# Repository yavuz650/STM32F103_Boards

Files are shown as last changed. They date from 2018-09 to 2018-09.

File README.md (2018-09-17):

# STM32F103 Boards
Rocket avionic boards, powered by the STM32F103C8T6 MCU.

This repository contains files and documentations of two avionic boards designed and developed for the Rocket Technologies Group of Istanbul Technical University in the year 2018. 

## Igniter Board
This board is designed to gather altitude data and control rocket's parachute deployment system. It was designed and programmed by Yavuz Selim Tozlu, assisted by Umit Yelken and L. Emre Top of Rocket Technologies Group.

## GPS Board
This board is designed to gather GPS data during flight, process it and send it to the ground station via the RF module attached to it. It was designed and programmed by Yavuz Selim Tozlu. 

Shout out goes to our [sponsor](http://www.megasistem.net) who was kind enough to manufacture the boards.

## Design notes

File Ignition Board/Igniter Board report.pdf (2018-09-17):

# STM32 Based

# Rocket Igniter Board

# Table of Contents

Preface | 3
Disclaimer | 3
About this document | 3
Feedback | 3
Further Reading | 3
PART A | Introduction to the board | 4
Chapter A1 | Purpose of this board | 5
Chapter A2 | Design process | 5
Chapter A3 | Board properties | 7
Chapter A4 | Post-manufacturing | 7
PART B | Embedding the STM32 MCU | 12
Chapter B1 | MCU Selection – Why STM32F103? | 13
Chapter B2 | External Circuitry | 13
Chapter B3 | Board Design | 15
PART C | Ignition Circuit | 17
Chapter C1 | The Circuit | 18
Chapter C2 | Safety Measures | 19
Chapter C3 | The Flaw | 19
PART D | Power Supply | 20
Chapter D1 | Step Down Regulator | 21
Chapter D2 | Linear Regulator and Power Switch | 21
PART E | Miscellaneous Parts | 22
Chapter E1 | MS5611 Barometer | 23
Chapter E2 | SD-Card Socket and Buzzer | 23
Final Words and Remarks | 24
About the Author | 24

# Preface

## Disclaimer

This document is written purely for guidance purposes. It is not written or verified by a professional. Everything shared in this document are of my own experience and observations. Therefore, the information might be incorrect or inaccurate. Reader must fully acknowledge this before moving forward.

## About this document

The purpose of this document is to share the experience and observations that were gathered during the design of this board with public, in order to ease hardware development for future generations. There is no exact target audience; students, hobbyists, even professionals may benefit from this. However, this document assumes the reader has basic knowledge of PCBs and electronics.

Release date: September, 2018

## Feedback

Any feedback related to the document or the design is welcome. Feel free to ask questions, suggest changes or improvement. Please direct your inquiries to tozlu16@itu.edu.tr.

## Further reading

Most of the knowledge in this document is derived from manuals and application notes from various companies. Below are the essential manuals and datasheets.

- https://www.st.com/resource/en/application_note/cd00164185.pdf
- https://www.st.com/resource/en/datasheet/cd00161566.pdf
- https://www.st.com/resource/en/reference_manual/CD00171190.pdf
- https://www.alldatasheet.com/datasheet-pdf/pdf/880802/TEC/MS5611-01BA03.html (https://www.alldatasheet.com/datasheet-pdf/pdf/880802/TEC/MS5611-01BA03.html)
- http://www.ti.com/lit/ds/symlink/lm2596.pdf

# PART A

# Introduction to the board

## A1) Purpose of this board

The Igniter Board was designed and developed for the Rocket Technologies Group of Istanbul Technical University. The board was designed to be included in the avionic bay of a rocket, and it eventually did fit inside the bay perfectly.

Its goal was to control and enable the deployment of the rocket’s parachute. The deployment process begins by estimating the altitude using the on-board embedded barometer. Upon reaching 20 meters below the apogee point, the board ignites two ignition wires, which in turn ignite an amount of black powder which ejects the surrounding body of the rocket to allow the parachute to be deployed.

Aside from ignition, it features a UART bridge, which is used to transmit altitude data, to another board in the bay.

## A2) Design process

The board consists of the following segments; MCU, barometer, ignition circuits, regulators and miscellaneous parts. All the drawings were done in Autodesk® Eagle 8.6.0. You might need 8.6.0 or later versions to open the board files.

The proper way of doing the schematic designs is to split the board up into modules like I did above, then work on modules, rather than working on the whole schematic all at once. For instance, I first drew the schematics of the MCU and did not move on to another part until I was done with it. After completing the MCU, I moved on to the regulators and so on. Modularizing the board makes it easier to maintain and manage the parts.

For this board, schematic design was basically reading and following the manuals. For this job, you will stick to the manuals that I shared in the preface section. Those manuals contain almost all the information you would need. The board layout, however, was somewhat trickier.

Due to budget limitations, the board had to be two-layered. Because of this, both layers had to contain a power plane and signal tracks. I decided to fill the top plane with GND and bottom plane with VDD. With this design, I ended up with a bunch of isolated sub-planes, as the signal tracks interrupt the power plane on that layer. Therefore, I routed lots of new, wide tracks that connect all the isolated planes with the main power plane. This is the problem with two-layered boards; dedicated layers for power planes are unavailable, instead power planes that are frequently interrupted by signal tracks must suffice. ST suggests to use at least a four-layered board to avoid this, though this two-layered board worked just fine.

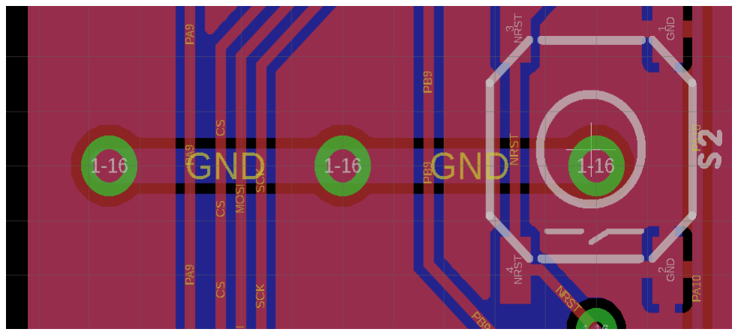
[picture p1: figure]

Figure 1: 0.8mm GND track routed to connect isolated planes

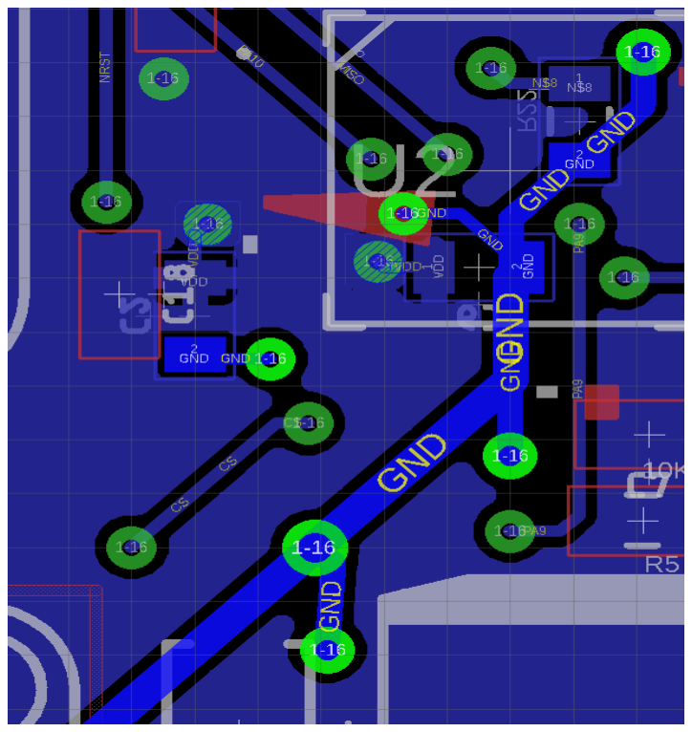
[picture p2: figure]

Figure 2: 0.7mm GND track routed to connect isolated planes

Layout of the parts was also challenging. Since the board was going to be housed in a rocket, I had very limited space. I had to keep the board as small as possible while also delivering the requirements. Finding the most optimized layout took several trials and errors, though it still is not perfect. My way of doing this was laying out and routing the MCU parts first, then moving on to ignition circuit and other miscellaneous parts. Throughout this process, I occasionally found myself having routing issues, this forced me to place parts on the bottom layer, as well as redesigning entire segments of the board. Ultimately, I managed to develop an optimal layout.

All the resistors and capacitors are of 0805 package. The only reason for this is that 0603 package is difficult to solder by hand, whereas 0805 is easier and also small enough for this board.

## A3) Board properties

- Board size | 69.50mm x 85.00mm
- Board thickness | 0.8mm, two-layered.
- Material | FR-4
- Soldermask | Green
- Track thickness | 1 oz (35um)

## A4) Post-manufacturing

Following images represent the three main phases of this board’s production in order; computer drawing, manufactured board, soldered board.

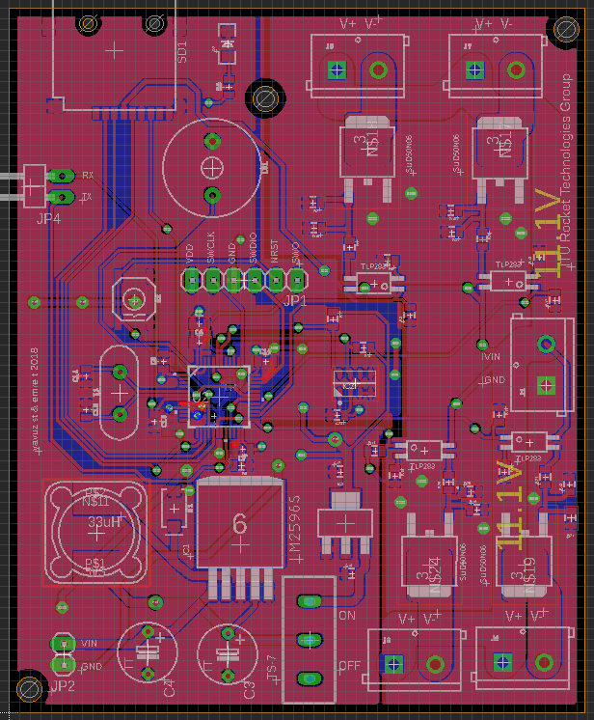
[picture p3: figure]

Figure 3: Computer drawing. Eagle 8.6.0

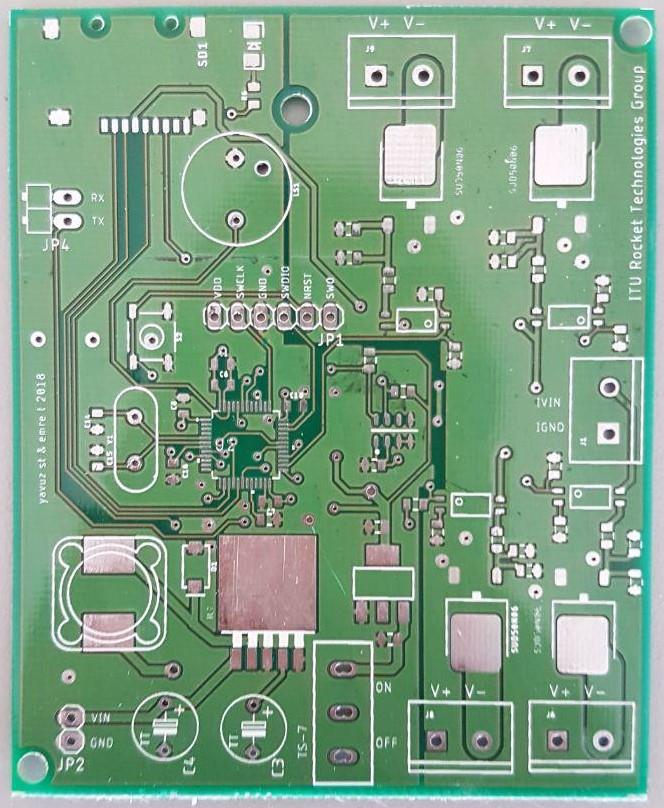
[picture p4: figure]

Figure 4: Manufactured board (top)

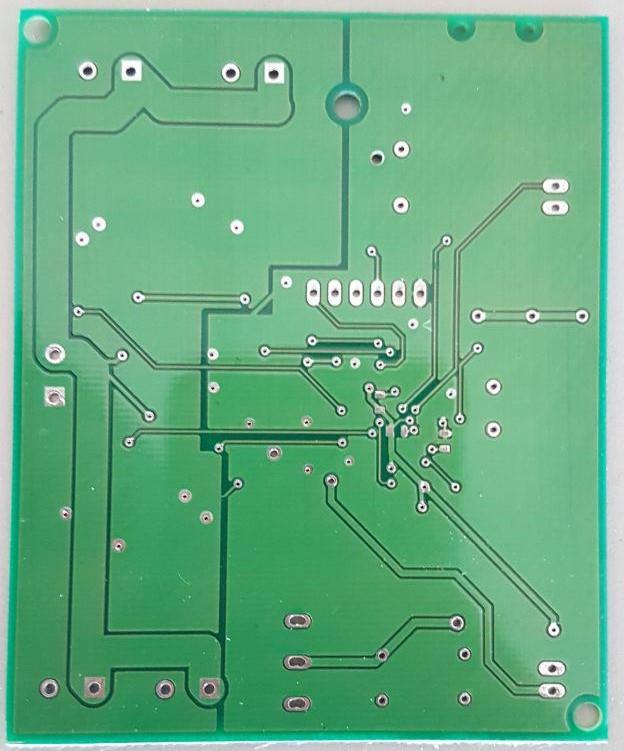
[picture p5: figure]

Figure 5: Manufactured board (bottom)

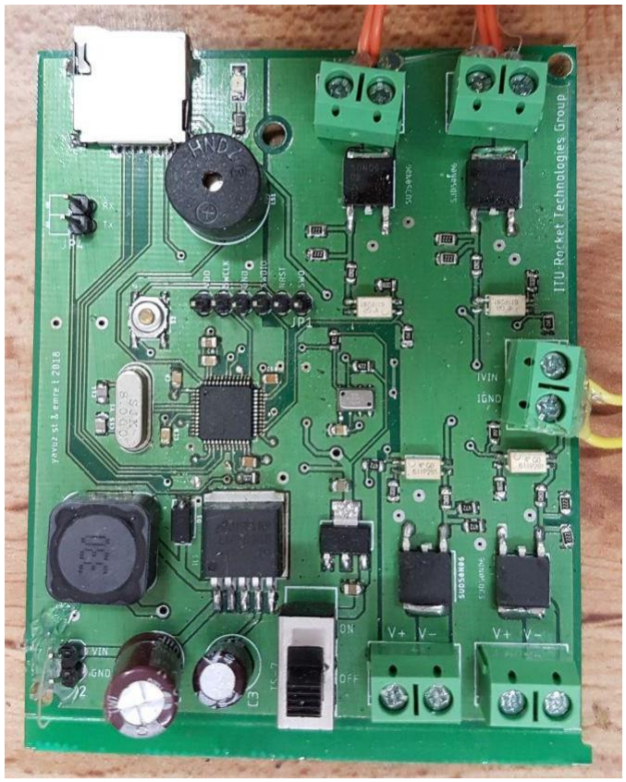
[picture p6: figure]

Figure 6: Soldered board (top)

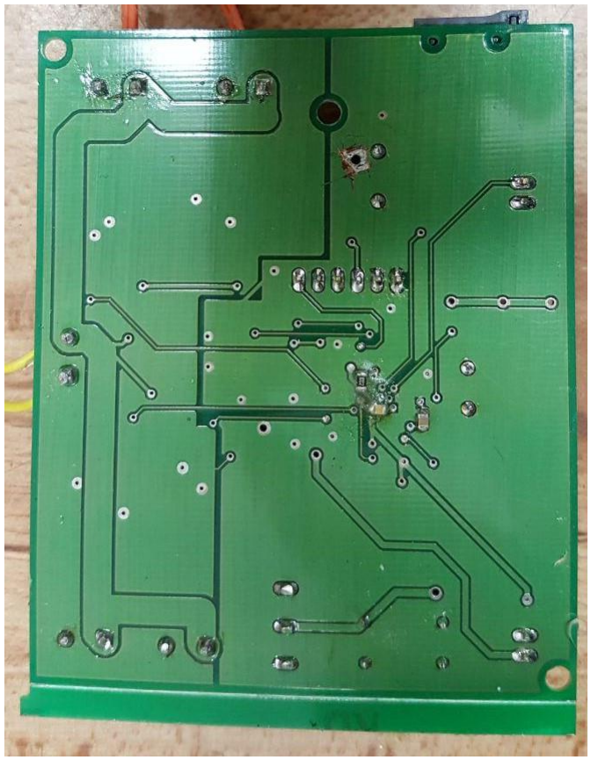
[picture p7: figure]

Figure 7: Soldered board (bottom)

This board is hand-soldered. There is visible flux residue left, especially on the bottom. I used Isopropyl alcohol to clean the top layer, perhaps due to the ingredients of my IPA, it left visible residue all over the board. An ESD safe brush was used to do the cleaning.

Reader may have noticed the hole with a scratched surrounding. That hole is a manufacturing flaw, it does not exist in the design. It is essentially a via that forms a conductive path between the top and the bottom layer, but around that area of the board, top layer is GND and bottom layer is VDD. This means that hole creates a short, this is why I had to scratch its surrounding copper to isolate it. I verified the short with a multimeter, checked all 6 boards that I received from the PCB house, all of them were suffering from the same flaw. This is a rare scenario where the PCB house manufactured defected boards.

# PART B

# Embedding the STM32 MCU

## B1) MCU Selection – Why STM32F103?

The main concerns during the MCU selection phase were; price, availability, software support, processing power, memory and physical size. At this point, options were quite clear; ATmega or STM32 – most common and easy to use MCUs in the market. Using ATmega was the easiest and the most reliable choice, however that would contradict with the idea of this project – which is to learn and experience new concepts, technologies. Today, developing projects with ATmega a.k.a. Arduino MCUs are incredibly simple, so much so that it merely gives people the illusion of actually developing something, which rarely is the case. This is mainly why the STM32 was chosen for this project.

The processing power that came with the STM32 was certainly not needed, neither was the memory, but the learning difference was immense.

Tools and libraries provided by ST incredibly eased up the software development phase, which placed STM32 above the other MCUs in the market.

## B2) External Circuitry

Minimum external parts to get the STM32 MCU working are; decoupling capacitors, a crystal, reset circuitry, boot pin configuration and SWD output. Note that, this is what ST suggests, indicating the MCU may work without some of those components. Also, an external crystal is not mandatory since the MCU offers an internal clock source. The drawbacks are that internal oscillator is less reliable, has more jittering and also less accurate than an external crystal.

Detailed information on decoupling caps can be found in the manual. To sum it up, for STM32F103C8T6 MCU, you would need; 5x 100nF, 1x 10uF, 1x 1uF decoupling capacitors to filter the power input. The MCU has 3 main power pairs, 1 analog power pair and 1 external battery input which should be connected to the VDD rail if not used.

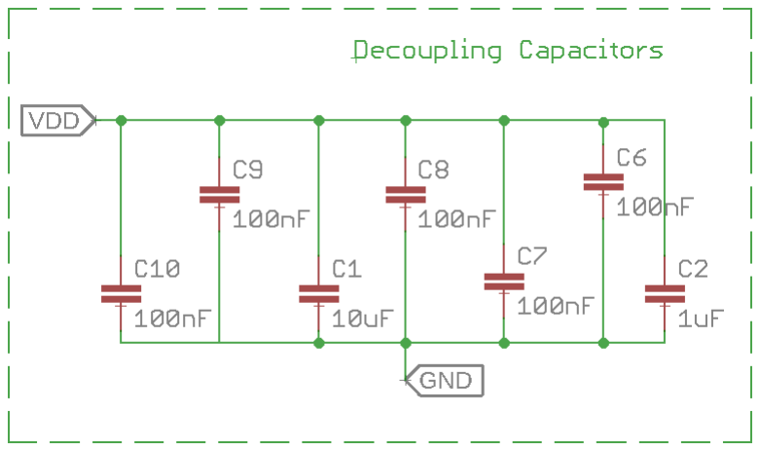
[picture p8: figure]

Figure 8: Decoupling capacitors for STM32F103C8T6

The memory block used to boot the MCU is determined by configuration of boot pins. Main flash memory is sufficient for most purposes, this project is no exception. Correct boot pin configuration for main flash memory is achieved when both boot pins are in low state, in other words, pulled to low. The manual suggests to use 10kOhm resistors as pull-downs.

In order to give the user the option to alter the boot mode between different memory blocks, designer can attach jumpers to the boot pins. Since this would take extra space on the board, I decided to strictly pull the pins low. Detailed information on boot pins can be found on the manual.

Igniter board houses an external crystal for the STM32 MCU. There is no guidance as to what the proper frequency would be, therefore an 8MHz crystal is used. The important thing here is to match the crystal’s frequency value with the value in your code during software development. Any value from 15pF to 22pF for load capacitors would be fine.

Reset circuitry is also described in the manual. Implementation for this board is shown in the following image.

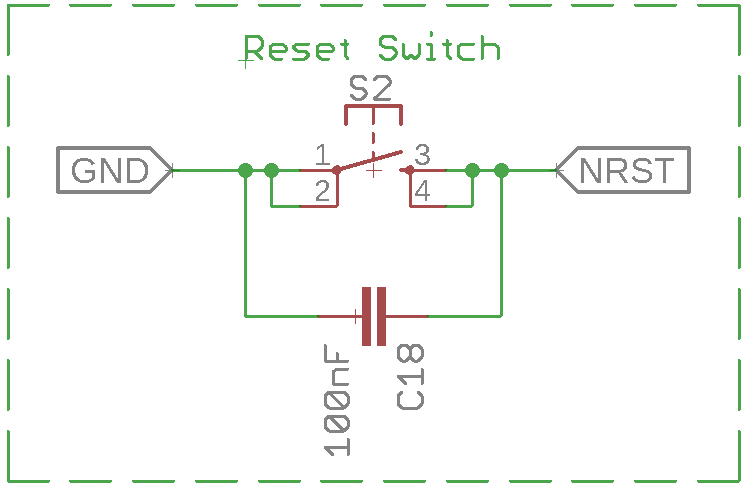
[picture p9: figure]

Figure 9: Reset Circuitry. NRST is tied to NRST pin of the MCU

As an interface between the MCU and the computer, Serial Wire Debug is used. Normally, SWD requires 3 pins; SWCLK, SWDIO, RST, aside from a common ground. On the Igniter Board, there are 2 additional pins; VDD and SWO.

VDD pin is added so that the board could be powered without having to use the main power supply of the board. This way I could power, program, debug the MCU without having to provide an external power source, which was really helpful during the programming and the testing phase.

SWO pin is an extra debugging feature offered by the SWD interface. Although it exists on the board, SWO pin was never used.

## B3) Board Design

There are lots of guides on placement of decoupling capacitors. Following image is taken from ST’s manual and suggests the most ideal placement, which I attempted to follow.

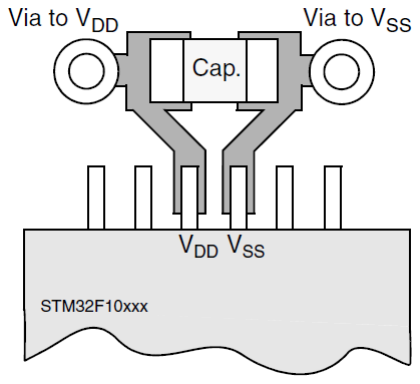
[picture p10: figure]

Figure 10: Ideal capacitor placement

To achieve this placement for each and every capacitor on a two-layer board is simply impossible, it is not required either. The idea is to keep the tracks as short and wide as possible, maintaining a low impedance. Also, both layers can be used to place those capacitors. On the Igniter Board, all the tracks entering the MCU are 0.25mm wide.

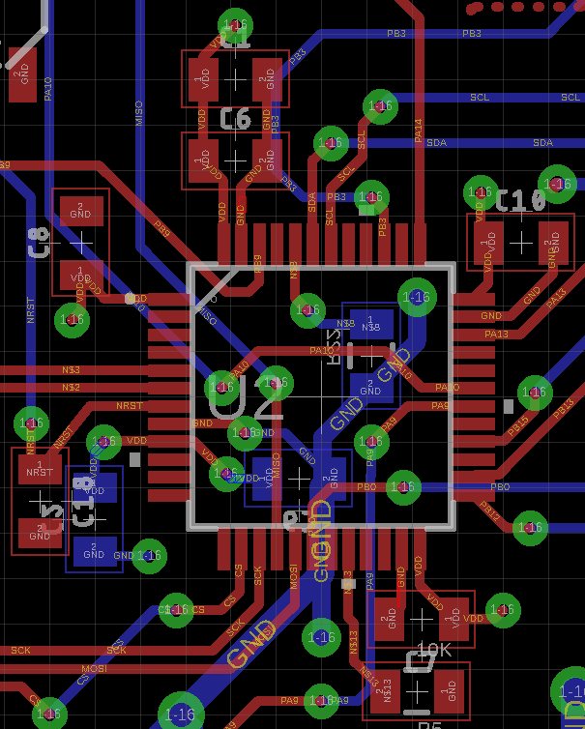
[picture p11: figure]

Figure 11: Circuitry around the STM32 MCU. Capacitors and resistors.

For the crystal, I kept it as close as possible to the MCU, while keeping the tracks and the load capacitors symmetric.

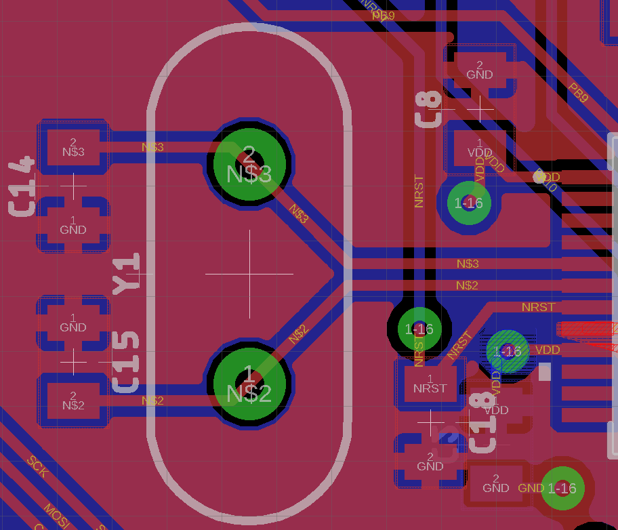
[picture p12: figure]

Figure 12: Symmetric tracks and capacitors for the crystal

It can be stated that the STM32 MCU was embedded properly and successfully on this board. No stability issues, timer inaccuracy or any other unexpected behavior were observed.

# PART C

# Ignition Circuit

## C1) About the circuit

Ignition circuit is the electronic system that controls the ejection of the rocket. Due to the nature of its task, it is crucial that the system is fail-safe. Thus, it is equipped with an array of components to attain the level of safety required. The last thing needed on the field is a rocket ejecting at the wrong time, in the wrong place i.e. on the ground. It must be noted that this circuit has an enormous flaw that will be addressed soon.

Following is an image of the schematic of the circuit.

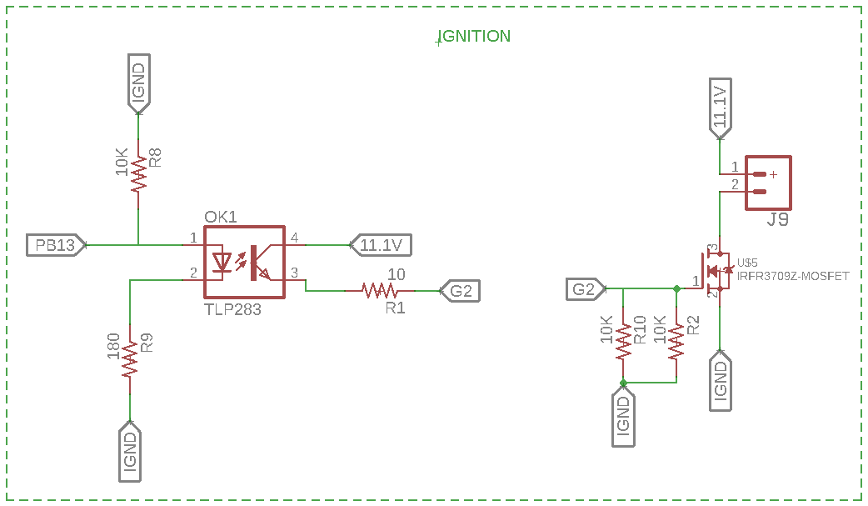
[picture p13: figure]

Figure 13: Ignition Circuit schematic

The circuit consists of two main stages: The opto-coupler and the N-MOSFET. Input of the opto-coupler’s LED is connected to the MCU’s pin PB13 in this case. The chain of events is triggered as the MCU drives the associated pin high, which activates the opto-coupler and ties 11.1V to the MOSFET’s gate. Applying voltage to the MOSFET’s gate allows current to flow from the drain to the source. Finally, this current flows through the terminal placed in between the drain and the source. Ignition wire that is attached to the terminal is ignited by this very current.

The circuit is powered directly from a 11.1V Li-Po battery, and has a separate ground(IGND). Cables for power input are attached to a terminal, since common pin headers cannot handle the power delivered by the battery.

During the ignition of the wire, current draw can go up to 5A. Thus, MOSFET used in this circuit must be able to handle currents up to 5A, voltages up to 12V. The MOSFET used in this board is SUD50N06 from Vishay.

## C2) Safety Measures

The ignition circuit is required to be electrically isolated from the rest of the board, as noise might cause the opto-coupler or the MOSFET to get activated or prevent them from getting activated, despite this is unlikely. Any possible kind of electrical interference between the circuit and the rest of the board is unwanted. This requirement led to the use of an opto-coupler. This way, the ignition circuit and the rest of the board do not have to share a common ground.

The input of the opto-coupler and the gate of the MOSFET are pulled to low. These pins cannot be left floating as this could lead to unintended activation of the components. Those pull-down resistors cannot be omitted. Notice, not one, but two pull-down resistors are attached to the gate of the MOSFET for further safety.

## C3) The Flaw

The design of this circuit contradicts with one of the main requirements discussed above, which is electrical isolation between the circuit and the rest of the board. Careful eyes may have noticed this just by looking at the schematic given at the beginning of this part.

The output of the diode inside the opto-coupler is tied to IGND through a resistor, whereas it should have been tied to GND. The reason can be obvious, the MCU’s 3.3V logic level is defined with respect to GND, not IGND. Then, only way to make this circuit work is to tie GND and IGND together, which makes the entire circuit pointless and redundant. Unfortunately, there is no alternative solution, and that is the work around I followed with my circuit.

Also, notice the pull-down resistor attached to the input of the opto-coupler pulls the pin to IGND, not GND –which is another flaw.

Nevertheless, this circuit did work with no problems, and successfully ejected the rocket’s body at the desired altitude.

Following is the corrected version of the circuit.

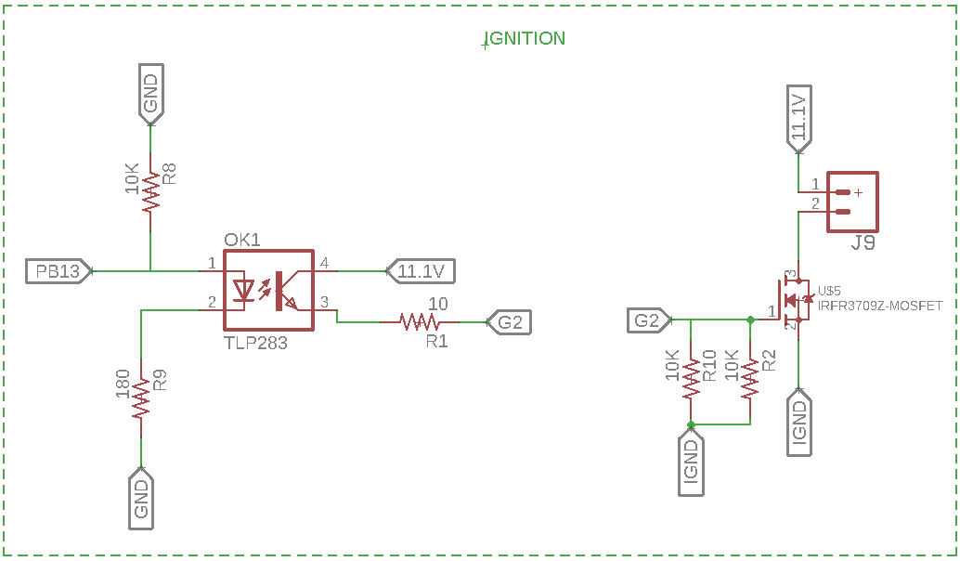
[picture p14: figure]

Figure 14: Corrected circuit.

# PART D

# POWER SUPPLY

## D1) Step Down Regulator

The input voltage for the circuit is planned to be 7.4V from a Li-Po battery. Target voltage is 3.3V. This leaves us two options, a linear regulator or a step down regulator. Regulating 7.4V to 3.3V with a bare linear regulator is very inefficient and slightly risky. Instead, I embedded a step down regulator to drop the 7.4V to 5V and use a linear regulator thereafter.

The step down regulator is based on the LM2596 from TI. The circuitry around it consists of an inductor, two aluminum capacitors and a schottky diode. This is also the suggested circuit in the datasheet.

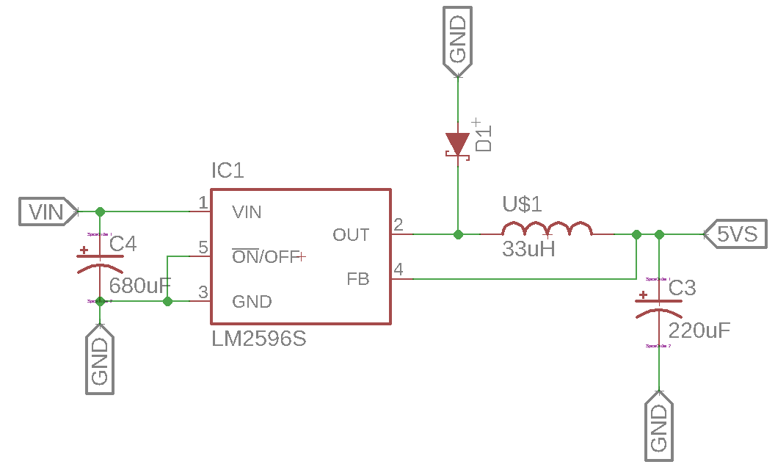
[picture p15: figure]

Figure 15: Step down regulator circuit, based on LM2596

There is no significant reason to use aluminum capacitors for this circuit, however, they are cheap and easily available.

As for the layout, TI pointed out some information in the datasheet, the rule of thumb is to keep the traces as wide as possible and the external circuitry close to the LM2596 IC.

## D2) Linear Regulator and Power Switch

To achieve the target voltage, a linear regulator is used to drop 5V to 3.3V. The linear regulator used in this board is AMS1117 from ams-semitech.

There is also a slide switch added to the board. This switch controls the whether the MCU side of the circuit is powered or not, it has nothing to do with the ignition circuitry.

There is a minor, yet silly design flaw about the switch’s placement. The current to the circuit enters the switch after it goes through the step down regulator. This means, the regulator is powered on and is working no matter what the state of the switch might be. This is why the switch should have been placed right after the power jack to function as it was intended.

It can be seen that the holes for the slide switch are not circular, as they usually are. They are rather oblong holes. This is a very important detail about the package of the switch. I drew the board symbol of the switch myself, mainly because there were no matching libraries. To draw oblong holes in Eagle, one has to use the “milling layer” in Eagle. The oblong hole should be drawn on the milling layer, and must be included in the gerber files that will be sent to the PCB house.

# PART E

# MISCALLENOUS PARTS

## E1) MS5611 Barometer

The board houses an MS5611 digital barometer from TE Connectivity. Its only task is to measure the air pressure, then convert it to an altitude value.

Schematic of the barometer includes a mere capacitor, and 2 I2C pull-up resistors, as is suggested by its datasheet.

The primal challenge with the barometer is, in fact, in the software side. That is, implementing C code for the communication between the STM32 MCU and the sensor. Enough information on software development with MS5611 is given on the datasheet. However, to realize a properly working interface takes some effort. A working library based on the HAL drivers from ST is shared in the repository.

## E2) SD Card Socket and Buzzer

One of the requirements of the igniter board was to save flight data to a micro-SD card attached to the board. However, despite many attempts, I never managed to establish a fully working interface between the MCU and the micro-SD card. Therefore, it is unknown whether the socket circuitry works at all. In spite of this, since it imitates working designs, I would expect it to function properly if a working interface is supplied.

The buzzer is a very specific component required due to the board’s purpose being related to the rocketry. Basically, when the rocket successfully lands on the ground, it needs to be located and retrieved by the team. Buzzer is added so that the sound it makes can be helpful to locate the parts.

There is a personal remark I would like to add about the buzzer’s circuitry. The buzzer is controlled and powered directly by the STM32 MCU. This is not the best way to do this, as the voltage supplied by the MCU is very low, 3.3V. Note that, the volume of the sound the buzzer makes is directly proportional to the voltage applied to its pins. Thus, a higher voltage is preferable in this case. To achieve this, a simple BJT can be used, with its base pin connected to the MCU.

## Final Words and Remarks

The development of this board involves months of research, a manufactured but unsuccessful board design, and lots of trials and errors. The very beginning of this process goes back to February of the year 2018. The board was successfully manufactured around July, 2018. This document is written during September, 2018.

It can be concluded that the board is successful. It was programmed, debugged, powered on and off many times, and has worked in a stable manner. It successfully gathered pressure and altitude data, ejected the rocket properly, as was intended. Nevertheless, reader should pay attention to the flaws mentioned throughout this document.

Most of the omitted information about the design can be deduced by the reader by carefully examining the board files.

Last but not least, the software that was used on this board for parachute deployment is shared in the repository.

## About the author

I am Yavuz Selim Tozlu, at the time of writing this paper, I am studying Electronics and Communication Engineering at Istanbul Technical University. E-mails in any regard can be sent to tozlu16@itu.edu.tr.

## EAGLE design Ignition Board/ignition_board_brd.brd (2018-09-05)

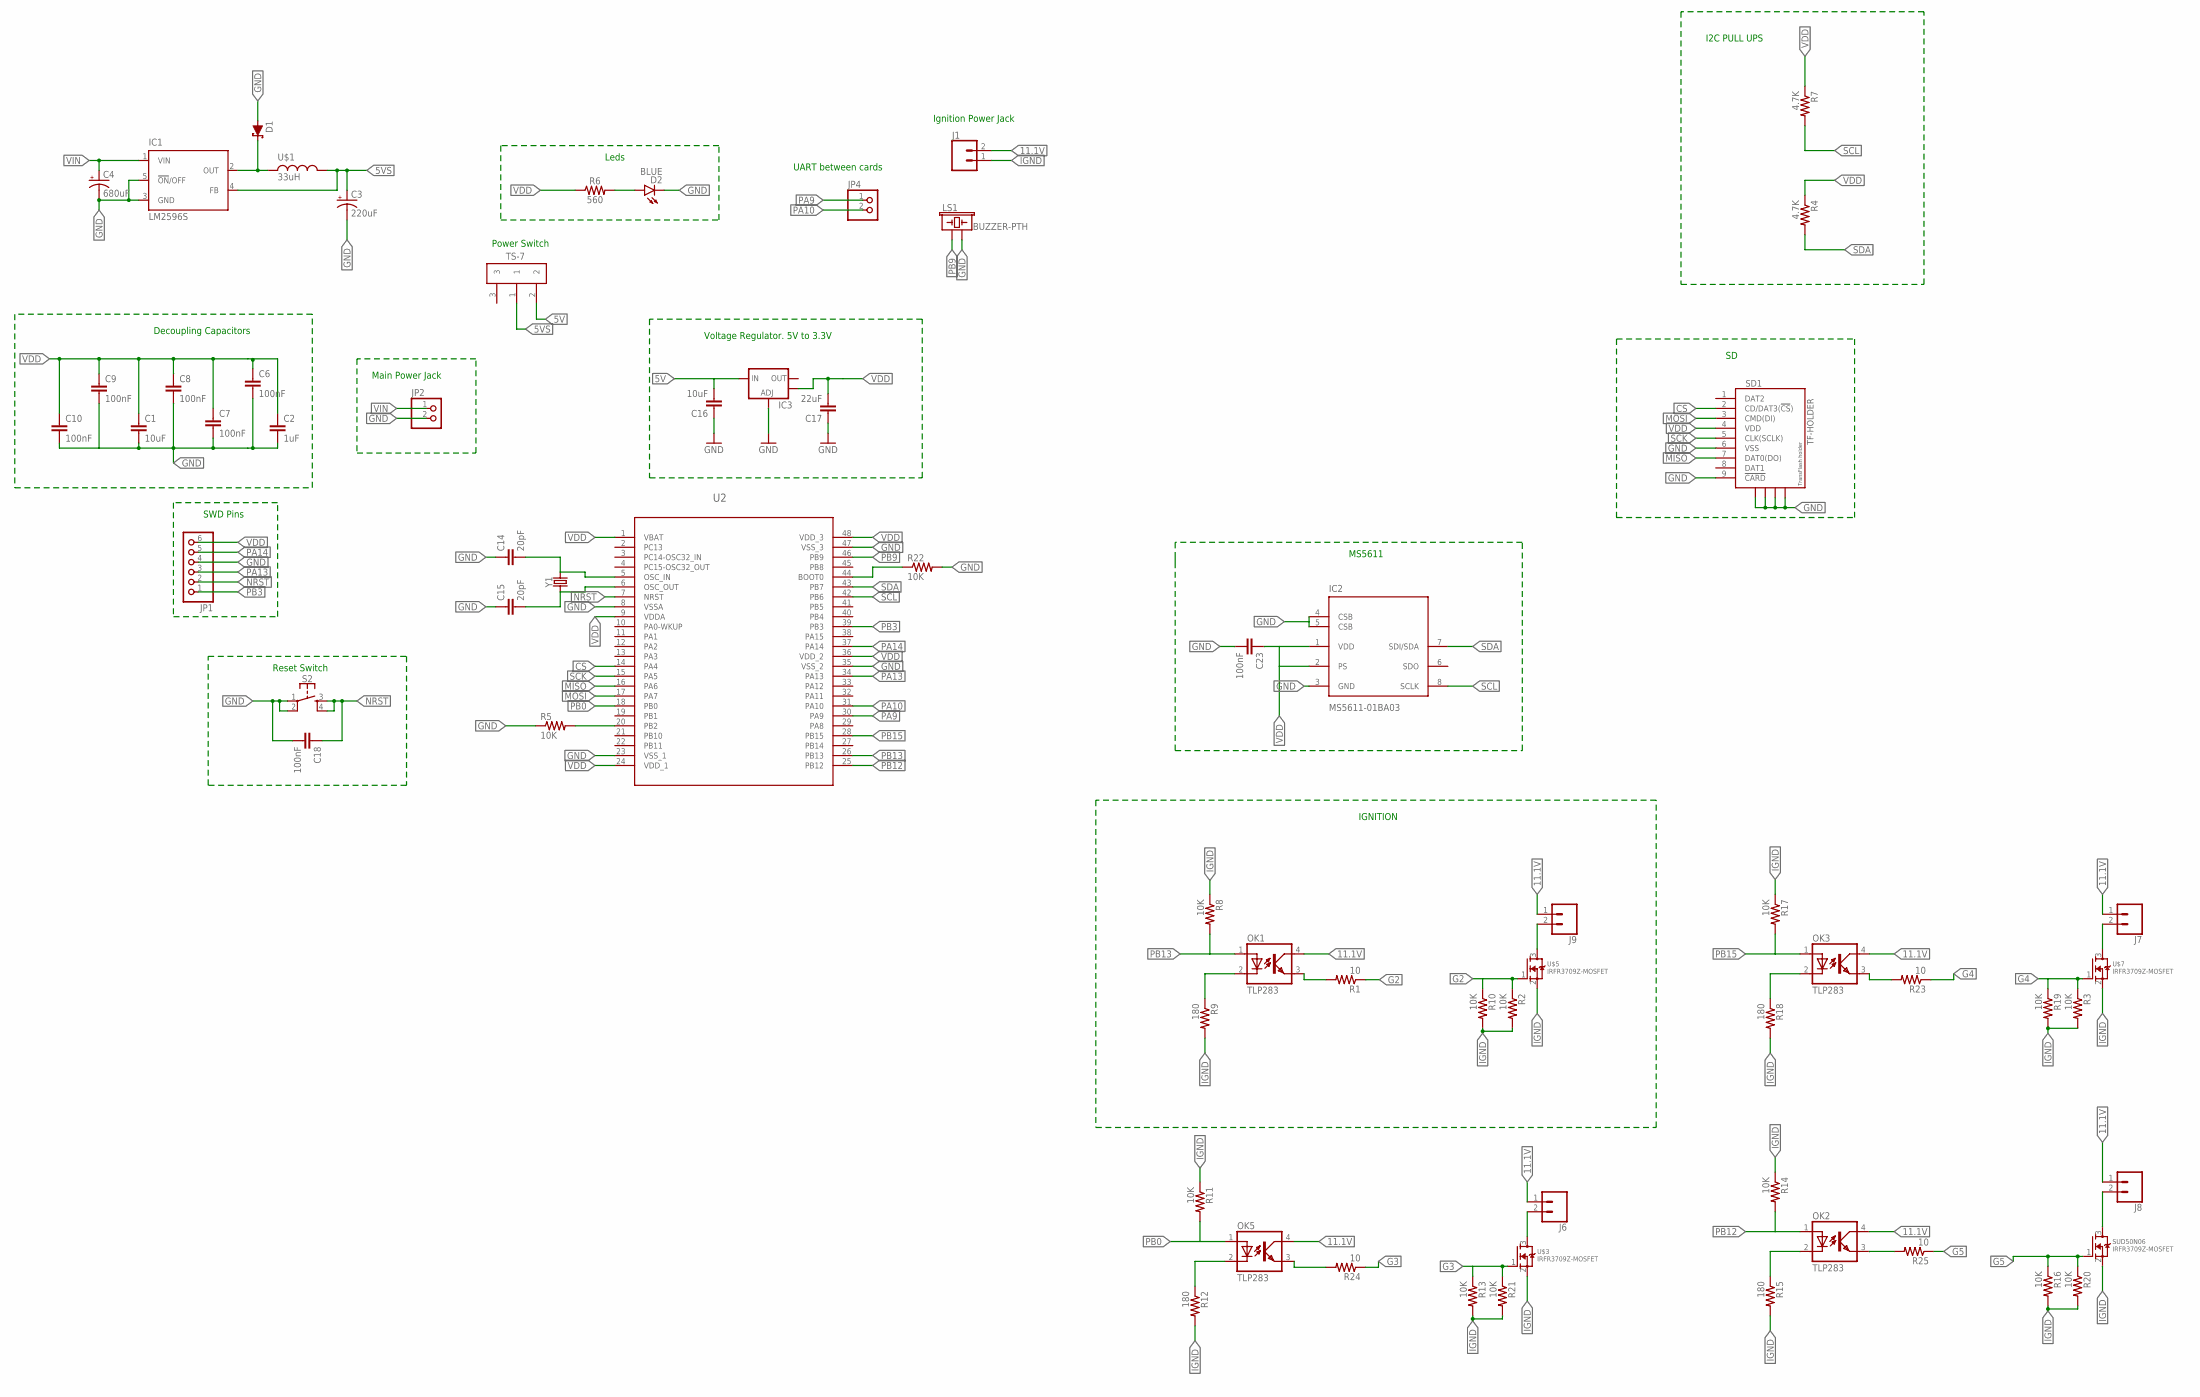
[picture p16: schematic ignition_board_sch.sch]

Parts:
C1: 10uF; 0805
C2: 1uF; 0805
C3: 220uF; TT5D7
C4: 680uF; TT5D7
C6, C7, C8, C9, C10, C18: 100nF; 0805
C14, C15: 20pF; 0805
C16: 10uF; 0805@2
C17: 22uF; 0805@2
C23: 100nF; 0805@2
D1: 3A/40V/500mV; SMA-DIODE
D2: BLUE; LED-1206
IC1: LM2596S; TO263-5
IC2: MS5611-01BA03; SON125P300X500X100-8N
IC3: V_REG_LM1117SOT223; SOT223
J1, J6, J7, J8, J9: CONN_025MM; SCREWTERMINAL-5MM-2
JP1: PINHD-1X6; 1X06
JP2: PINHD-1X2; 1X02
JP4: PINHD-1X2/90; 1X02/90
LS1: BUZZER-PTH; BUZZER-12MM
OK1, OK2, OK3, OK5: TLP283; MINI-FLAT-4
R1, R23, R24, R25: 10; 0805
R2, R3, R5, R8, R10, R11, R13, R14, R16, R17, R19, R20, R21, R22: 10K; 0805
R4, R7: 4.7K; 0805
R6: 560; 0805@1
R9, R12, R15, R18: 180; 0805
S2: MOMENTARY-SWITCH-SPST-2-SMD-5.2MM; TACTILE_SWITCH_SMD_5.2MM
SD1: TF-HOLDER; TF-PULL
SUD50N06: IRFR3709Z-MOSFET; TO252
TS-7: TS-7; TS7
U2: STM32F103CXT2; LQFP48-7X7MM
U$1: 33uH; MSS1260
U$3, U$5, U$7: IRFR3709Z-MOSFET; TO252
Y1: CRYSTALPTH-HC49US; HC49US

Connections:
5V: C16.2, IC3.3 (IN), TS-7.2
5VS: C3.+, IC1.4 (FB), TS-7.1, U$1.P$1
11.1V: J1.2, J6.1, J7.1, J8.1, J9.1, OK1.4 (COL), OK2.4 (COL), OK3.4 (COL), OK5.4 (COL)
CS: SD1.2 (CD/DAT3(!CS!)), U2.14 (PA4)
G2: R1.1, R2.1, R10.1, U$5.1 (G)
G3: R13.1, R21.1, R24.1, U$3.1 (G)
G4: R3.1, R19.1, R23.1, U$7.1 (G)
G5: R16.1, R20.1, R25.1, SUD50N06.1 (G)
GND: C1.2, C2.2, C3.-, C4.-, C6.2, C7.2, C8.2, C9.2, C10.2, C14.1, C15.1, C16.1, C17.1, C18.2, C23.2, D1.A, D2.C, IC1.3 (GND), IC1.5 (!ON!/OFF), IC2.3 (GND), IC2.4 (CSB), IC2.5 (CSB), IC3.1 (ADJ), JP1.4, JP2.2, LS1.- (2), R5.1, R22.2, S2.1, S2.2, SD1.6 (VSS), SD1.9 (!CARD), SD1.S1, SD1.S2, SD1.S3, SD1.S4, U2.8 (VSSA), U2.23 (VSS_1), U2.35 (VSS_2), U2.47 (VSS_3)
IGND: J1.1, R2.2, R3.2, R8.1, R9.2, R10.2, R11.1, R12.2, R13.2, R14.1, R15.2, R16.2, R17.1, R18.2, R19.2, R20.2, R21.2, SUD50N06.2 (S), U$3.2 (S), U$5.2 (S), U$7.2 (S)
MISO: SD1.7 (DAT0(DO)), U2.16 (PA6)
MOSI: SD1.3 (CMD(DI)), U2.17 (PA7)
unnamed: C15.2, U2.6 (OSC_OUT), Y1.1
unnamed: C14.2, U2.5 (OSC_IN), Y1.2
unnamed: R22.1, U2.44 (BOOT0)
unnamed: D1.C, IC1.2 (OUT), U$1.P$2
unnamed: OK1.3 (EMIT), R1.2
unnamed: R5.2, U2.20 (PB2)
unnamed: D2.A, R6.2
unnamed: OK2.3 (EMIT), R25.2
unnamed: J7.2, U$7.3 (D)
unnamed: J9.2, U$5.3 (D)
unnamed: J6.2, U$3.3 (D)
unnamed: OK3.3 (EMIT), R23.2
unnamed: OK5.2 (C), R12.1
unnamed: OK5.3 (EMIT), R24.2
unnamed: J8.2, SUD50N06.3 (D)
unnamed: OK2.2 (C), R15.1
unnamed: OK1.2 (C), R9.1
unnamed: OK3.2 (C), R18.1
NRST: C18.1, JP1.2, S2.3, S2.4, U2.7 (NRST)
PA9: JP4.1, U2.30 (PA9)
PA10: JP4.2, U2.31 (PA10)
PA13: JP1.3, U2.34 (PA13)
PA14: JP1.5, U2.37 (PA14)
PB0: OK5.1 (A), R11.2, U2.18 (PB0)
PB3: JP1.1, U2.39 (PB3)
PB9: LS1.+ (1), U2.46 (PB9)
PB12: OK2.1 (A), R14.2, U2.25 (PB12)
PB13: OK1.1 (A), R8.2, U2.26 (PB13)
PB15: OK3.1 (A), R17.2, U2.28 (PB15)
SCK: SD1.5 (CLK(SCLK)), U2.15 (PA5)
SCL: IC2.8 (SCLK), R7.2, U2.42 (PB6)
SDA: IC2.7 (SDI/SDA), R4.2, U2.43 (PB7)
VDD: C1.1, C2.1, C6.1, C7.1, C8.1, C9.1, C10.1, C17.2, C23.1, IC2.1 (VDD), IC2.2 (PS), IC3.4 (OUT), JP1.6, R4.1, R6.1, R7.1, SD1.4 (VDD), U2.1 (VBAT), U2.9 (VDDA), U2.24 (VDD_1), U2.36 (VDD_2), U2.48 (VDD_3)
VIN: C4.+, IC1.1 (VIN), JP2.1

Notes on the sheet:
Decoupling Capacitors
Voltage Regulator. 5V to 3.3V
Main Power Jack
Reset Switch
Leds
SWD Pins
MS5611
IGNITION
I2C PULL UPS
UART between cards
Power Switch
Ignition Power Jack

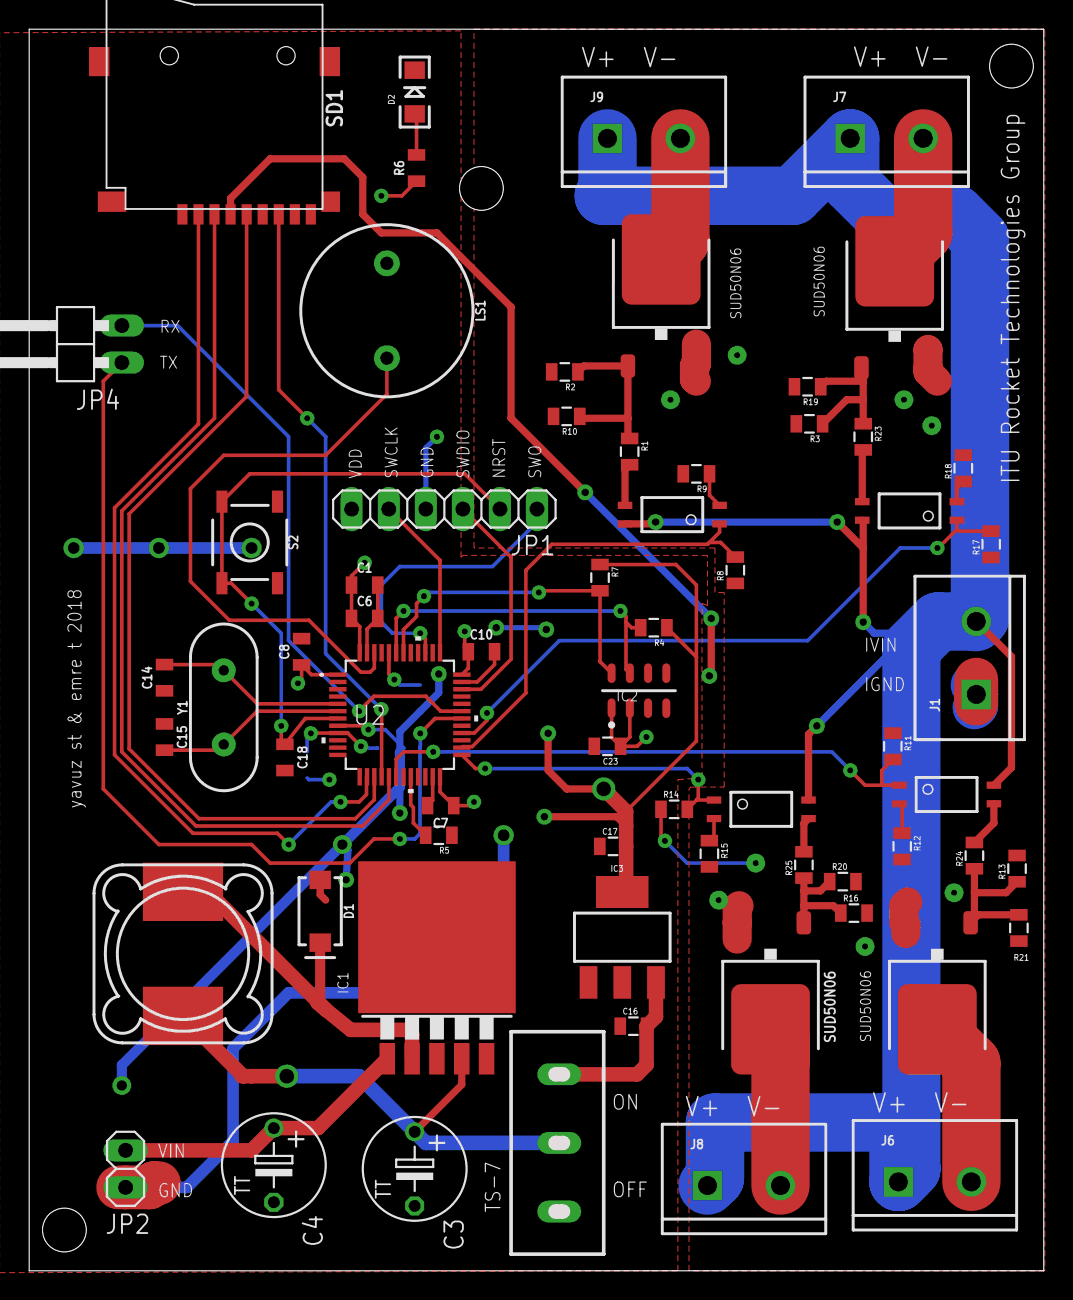
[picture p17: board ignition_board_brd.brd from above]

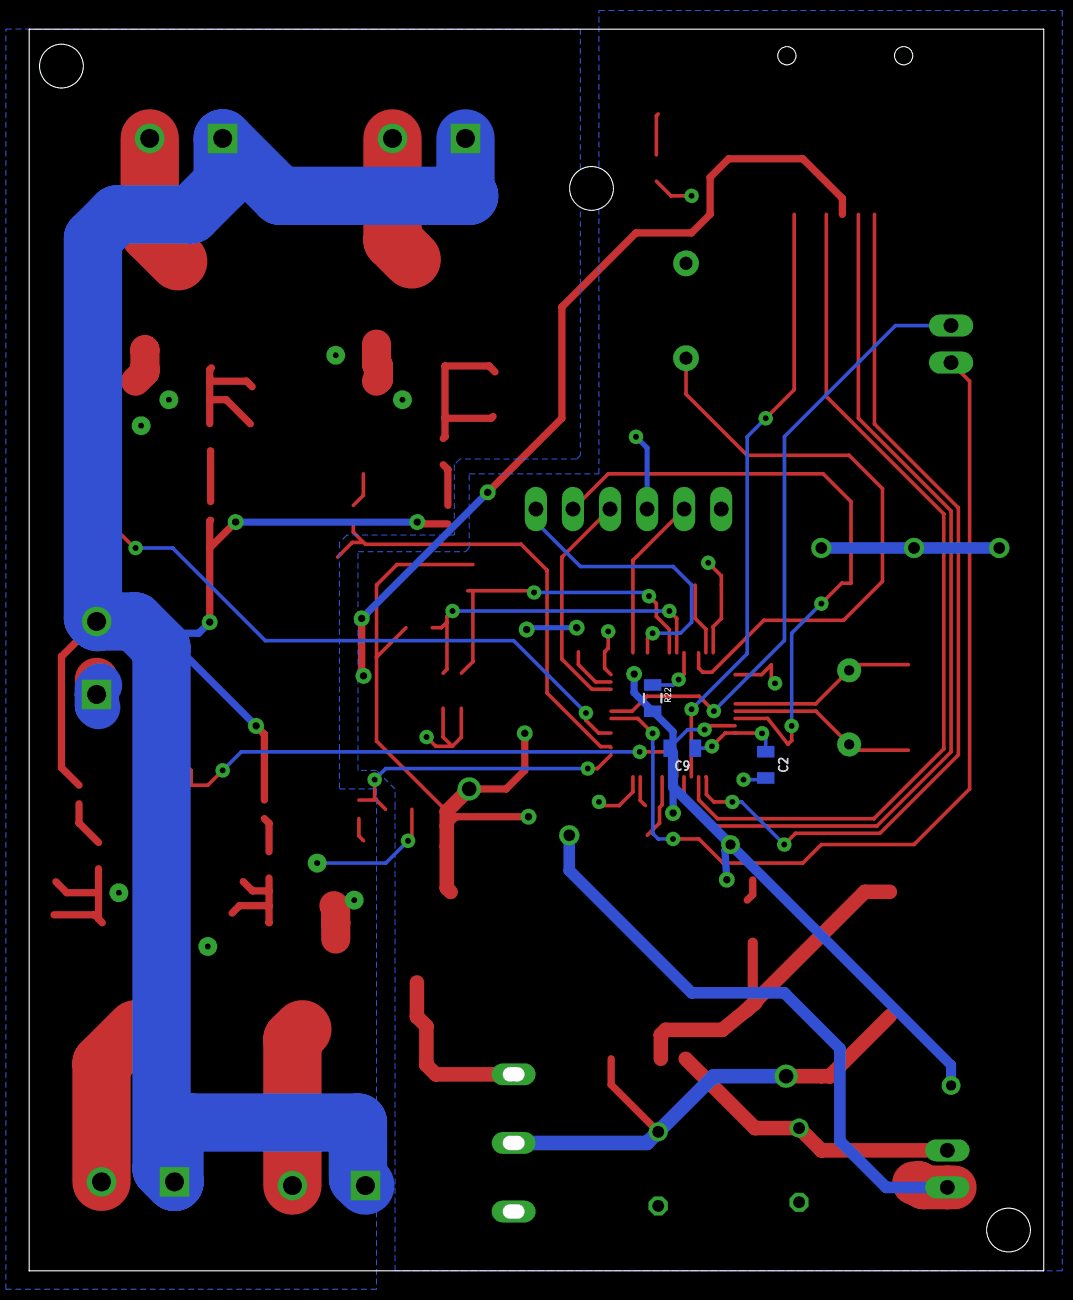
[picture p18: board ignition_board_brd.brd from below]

Board: 2 copper layers, 69.5 x 85.1 mm, 68 parts (3 on the bottom side), 46 nets.

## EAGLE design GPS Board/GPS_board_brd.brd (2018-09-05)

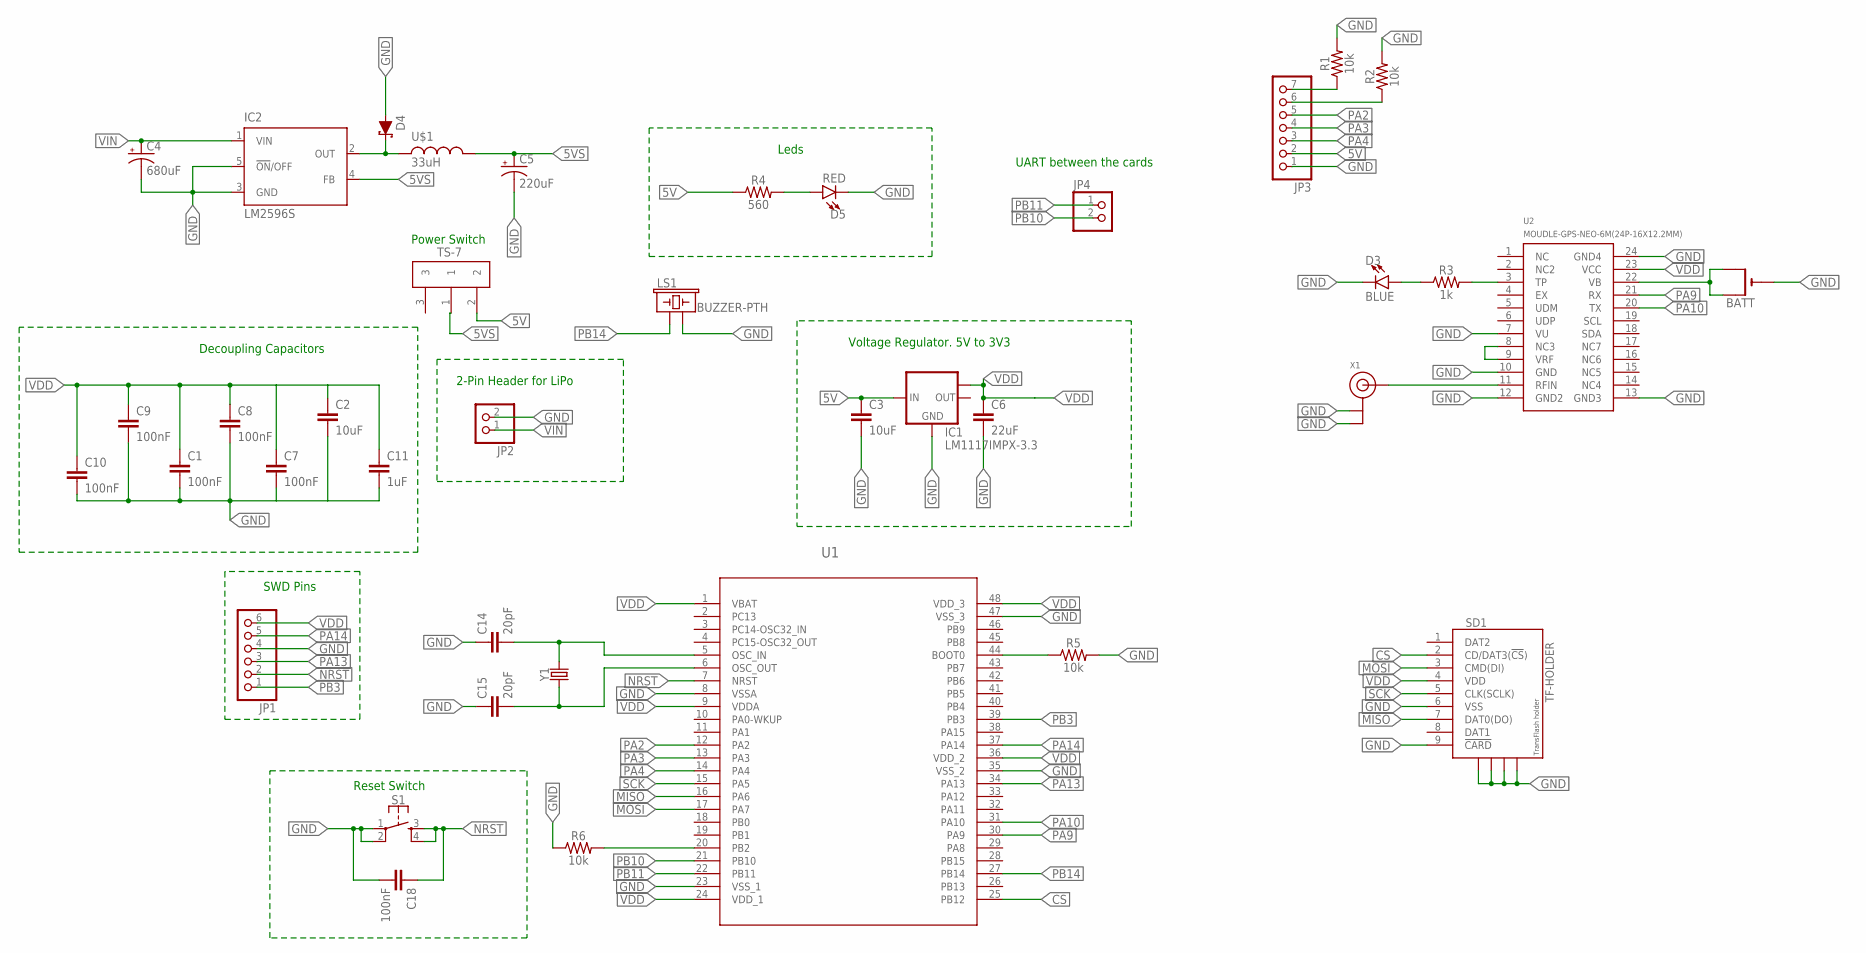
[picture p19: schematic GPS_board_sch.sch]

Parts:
BATT: CR1220SMT; CR1220-SMD
C1, C7, C8, C9, C10, C18: 100nF; 0805
C2, C3: 10uF; 0805
C4: 680uF; TT5D7
C5: 220uF; TT5D7
C6: 22uF; 0805
C11: 1uF; 0805
C14, C15: 20pF; 0805
D3: BLUE; LED-1206
D4: 3A/40V/500mV; SMA-DIODE
D5: RED; LED-1206
IC1: LM1117IMPX-3.3; SOT223
IC2: LM2596S; TO263-5
JP1: PINHD-1X6; 1X06
JP2: PINHD-1X2; 1X02
JP3: PINHD-1X7; 1X07
JP4: PINHD-1X2/90; 1X02/90
LS1: BUZZER-PTH; BUZZER-12MM
R1, R2, R5, R6: 10k; 0805
R3: 1k; 0805
R4: 560; 0805
S1: MOMENTARY-SWITCH-SPST-2-SMD-5.2MM; TACTILE_SWITCH_SMD_5.2MM
SD1: TF-HOLDER; TF-PULL
TS-7: TS-7; TS7
U1: STM32F103CXT2; LQFP48-7X7MM
U2: MOUDLE-GPS-NEO-6M(24P-16X12.2MM); GPS24P-SMD-1.1-16X12.2MM
U$1: 33uH; MSS1260
X1: ANTENNA_U.FL; U.FL
Y1: CRYSTALPTH-HC49US; HC49US

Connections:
5V: C3.1, IC1.3 (IN), JP3.2, R4.1, TS-7.2
5VS: C5.+, IC2.4 (FB), TS-7.1, U$1.P$1
CS: SD1.2 (CD/DAT3(!CS!)), U1.25 (PB12)
GND: BATT.-, C1.2, C2.2, C3.2, C4.-, C5.-, C6.2, C7.2, C8.2, C9.2, C10.2, C11.2, C14.1, C15.1, C18.2, D3.C, D4.A, D5.C, IC1.1 (GND), IC2.3 (GND), IC2.5 (!ON!/OFF), JP1.4, JP2.2, JP3.1, LS1.- (2), R1.2, R2.2, R5.2, R6.1, S1.1, S1.2, SD1.6 (VSS), SD1.9 (!CARD), SD1.S1, SD1.S2, SD1.S3, SD1.S4, U1.8 (VSSA), U1.23 (VSS_1), U1.35 (VSS_2), U1.47 (VSS_3), U2.7 (VU), U2.10 (GND), U2.12 (GND2), U2.13 (GND3), U2.24 (GND4), X1.1 (GND), X1.2 (GND)
MISO: SD1.7 (DAT0(DO)), U1.16 (PA6)
MOSI: SD1.3 (CMD(DI)), U1.17 (PA7)
unnamed: C14.2, U1.5 (OSC_IN), Y1.2
unnamed: C15.2, U1.6 (OSC_OUT), Y1.1
unnamed: BATT.+$1 (+), BATT.+$2 (+1), U2.22 (VB)
unnamed: U2.11 (RFIN), X1.3 (SIGNAL)
unnamed: R5.1, U1.44 (BOOT0)
unnamed: R6.2, U1.20 (PB2)
unnamed: D4.C, IC2.2 (OUT), U$1.P$2
unnamed: D5.A, R4.2
unnamed: U2.8 (NC3), U2.9 (VRF)
unnamed: R3.2, U2.3 (TP)
unnamed: D3.A, R3.1
unnamed: JP3.7, R1.1
unnamed: JP3.6, R2.1
NRST: C18.1, JP1.2, S1.3, S1.4, U1.7 (NRST)
PA2: JP3.5, U1.12 (PA2)
PA3: JP3.4, U1.13 (PA3)
PA4: JP3.3, U1.14 (PA4)
PA9: U1.30 (PA9), U2.21 (RX)
PA10: U1.31 (PA10), U2.20 (TX)
PA13: JP1.3, U1.34 (PA13)
PA14: JP1.5, U1.37 (PA14)
PB3: JP1.1, U1.39 (PB3)
PB10: JP4.2, U1.21 (PB10)
PB11: JP4.1, U1.22 (PB11)
PB14: LS1.+ (1), U1.27 (PB14)
SCK: SD1.5 (CLK(SCLK)), U1.15 (PA5)
VDD: C1.1, C2.1, C6.1, C7.1, C8.1, C9.1, C10.1, C11.1, IC1.TAB (OUT1), JP1.6, SD1.4 (VDD), U1.1 (VBAT), U1.9 (VDDA), U1.24 (VDD_1), U1.36 (VDD_2), U1.48 (VDD_3), U2.23 (VCC)
VIN: C4.+, IC2.1 (VIN), JP2.1

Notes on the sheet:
Decoupling Capacitors
Voltage Regulator. 5V to 3V3
2-Pin Header for LiPo
Reset Switch
Leds
SWD Pins
UART between the cards
Power Switch

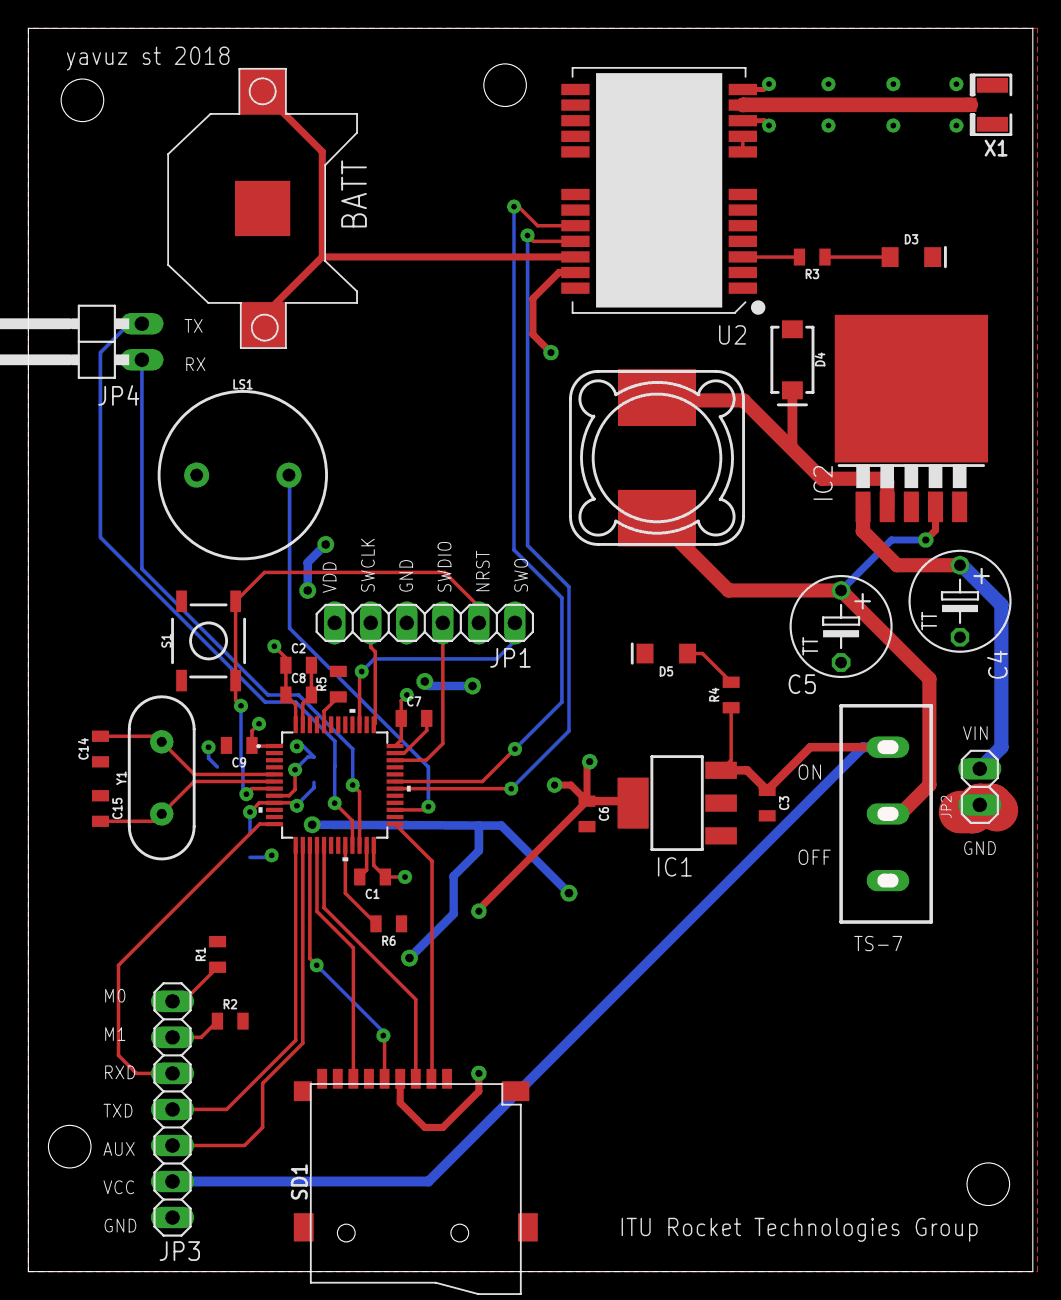
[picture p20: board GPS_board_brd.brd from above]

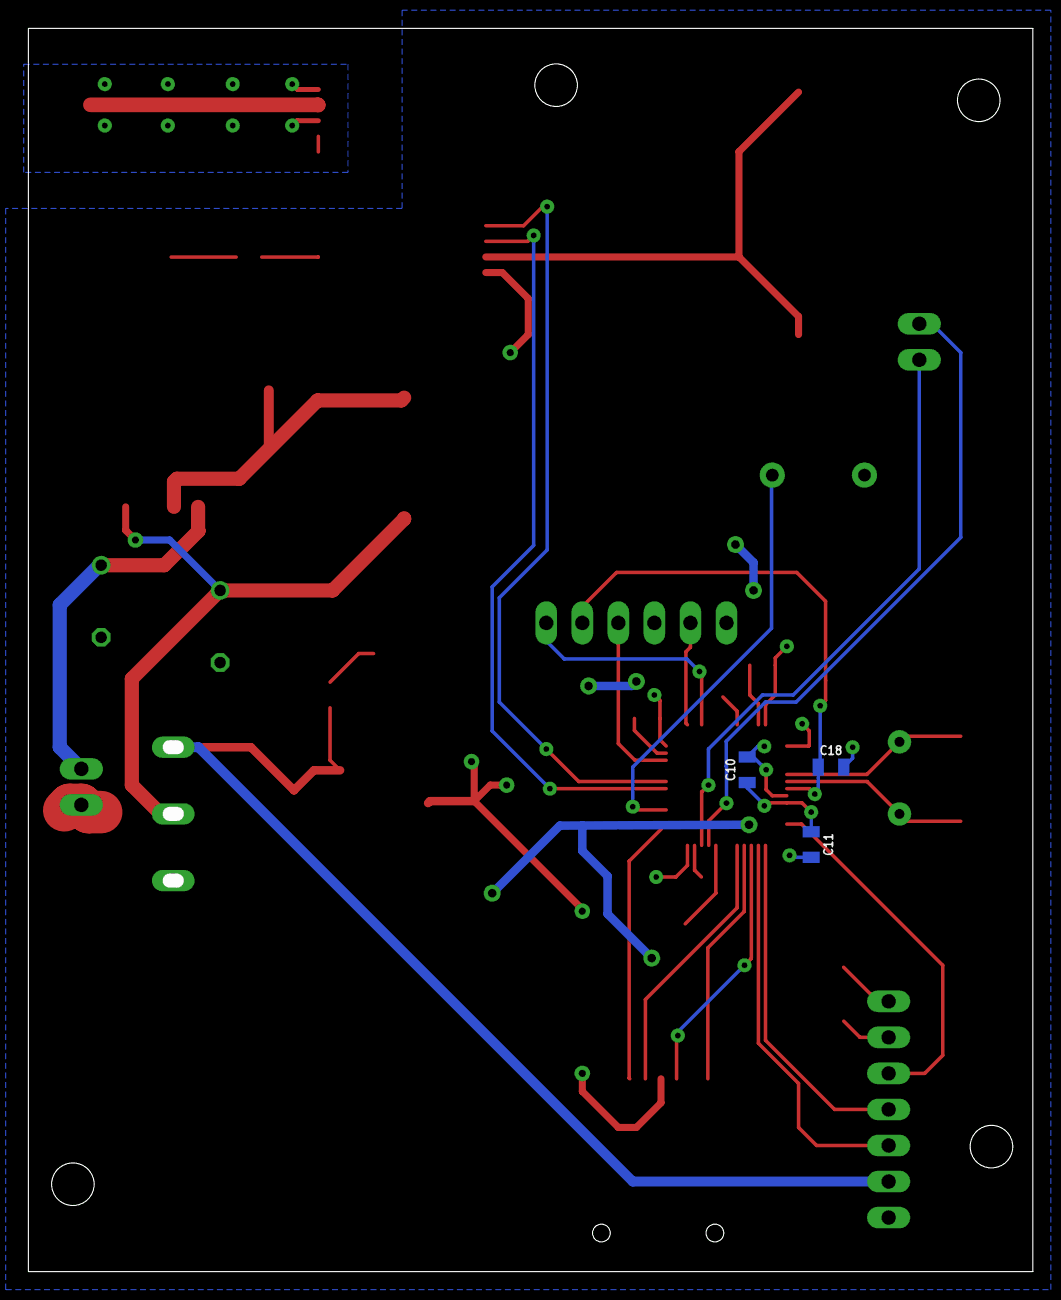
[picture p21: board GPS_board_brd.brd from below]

Board: 2 copper layers, 70.8 x 87.6 mm, 39 parts (3 on the bottom side), 34 nets.

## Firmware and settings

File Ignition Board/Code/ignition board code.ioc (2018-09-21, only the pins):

Mcu.UserName=STM32F103C8Tx
PA10.Signal=USART1_RX
PA13.Signal=SYS_JTMS-SWDIO
PA14.Signal=SYS_JTCK-SWCLK
PA4.Signal=GPIO_Output
PA5.Signal=SPI1_SCK
PA6.Signal=SPI1_MISO
PA7.Signal=SPI1_MOSI
PA9.Signal=USART1_TX
PB0.Signal=GPIO_Output
PB12.Signal=GPIO_Output
PB13.Signal=GPIO_Output
PB15.Signal=GPIO_Output
PB6.Signal=I2C1_SCL
PB7.Signal=I2C1_SDA
PB9.Signal=GPIO_Output
PD0-OSC_IN.Signal=RCC_OSC_IN
PD1-OSC_OUT.Signal=RCC_OSC_OUT

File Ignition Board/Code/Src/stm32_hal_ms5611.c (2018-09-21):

//includes *-----------------------------------------------------*
#include <stm32_hal_ms5611.h>

/** @defgroup MS5611 private function definitions
  * @{
  */

MS_Status Read_Prom(MS5611_Type *device)
{
	for(int i=1;i<7;i++) //iterate through coefficient addresses.
		{
			if(HAL_I2C_Mem_Read(device->i2c_bus,DEV_ADD,CMD_PROM_RD+2*i,1,device->prom_read_buf,2,20)!=HAL_OK)// save it to the prom buffer.
			{
				return MS_ERROR;
			}
			device->C[i-1] = (device->prom_read_buf[0] << 8) + device->prom_read_buf[1]; // calculate the coefficient from two seperate bytes.
		}
		
		return MS_OK;
}

void Get_Raw_Temp(MS5611_Type *device)
{
	uint8_t D2_adc_cmd_4096 = 0x58; //D2 ADC conversion command with 4096 oversampling rate
	
	HAL_I2C_Master_Transmit(device->i2c_bus,DEV_ADD,&D2_adc_cmd_4096,1,20); //send adc command
	HAL_Delay(50); //wait for the conversion to complete.
	HAL_I2C_Mem_Read(device->i2c_bus,DEV_ADD,CMD_ADC_READ,1,device->adc_read_buf,3,20); //read the adc result.
	
	device->D2 = (device->adc_read_buf[0] << 16) + (device->adc_read_buf[1] << 8) + device->adc_read_buf[2]; //calculate D2
}

void Calculate_Actual_Temp(MS5611_Type *device)
{
	device->dT = device->D2 - device->C[4]*pow(2,8);
	device->TEMP = (2000+device->dT*device->C[5]/pow(2,23))/100;
}

void Get_Raw_Pres(MS5611_Type *device)
{
	uint8_t D1_adc_cmd_4096 = 0x48; //D1 ADC conversion command with 4096 oversampling rate
	
	HAL_I2C_Master_Transmit(device->i2c_bus,DEV_ADD,&D1_adc_cmd_4096,1,20); //send adc command
	HAL_Delay(50); //wait for the conversion to complete.
	HAL_I2C_Mem_Read(device->i2c_bus,DEV_ADD,CMD_ADC_READ,1,device->adc_read_buf,3,20); //read the adc result.
	
	device->D1 = (device->adc_read_buf[0] << 16) + (device->adc_read_buf[1] << 8) + device->adc_read_buf[2]; //calculate D1
}

void Calculate_Actual_Pres(MS5611_Type *device)
{
	device->OFF = device->C[1]*pow(2,16) + (device->C[3]*device->dT)/pow(2,7);
	device->SENS = device->C[0]*pow(2,15) + (device->C[2]*device->dT)/pow(2,8);
	
	device->P = (device->D1*device->SENS/pow(2,21)-device->OFF)/pow(2,15); //pressure in pascal. divide by 100 to get mbar.
}

/**
  * @}
  */

/** @defgroup MS5611 public function definitions
  * @{
  */
MS_Status MS5611_Init(MS5611_Type *device, I2C_HandleTypeDef* i2c_handle)
{
	device->i2c_bus = i2c_handle;
	return Read_Prom(device);
}

float Return_Temp(MS5611_Type *device)
{
	Get_Raw_Temp(device);
	Calculate_Actual_Temp(device);
	return device->TEMP;
}
float Return_Pres(MS5611_Type *device)
{
	Get_Raw_Pres(device);
	Calculate_Actual_Pres(device);
	return device->P;
}
double Return_Altitude(MS5611_Type *device)
{
	Return_Temp(device);
	Return_Pres(device);
	return 4946.55*(8.96196-pow(device->P,0.190263));
}


/**
  * @}
  */

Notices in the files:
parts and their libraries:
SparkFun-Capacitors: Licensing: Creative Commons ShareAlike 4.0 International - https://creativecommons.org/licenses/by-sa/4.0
